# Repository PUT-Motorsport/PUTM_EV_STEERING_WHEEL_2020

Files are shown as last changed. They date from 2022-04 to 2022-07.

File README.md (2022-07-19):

# PUTM_EV_STEERING_WHEEL_2022

An overview of how I see this thing working:
kiera_schemat_blokowy_v2 (1)

* ~~Data gathered from IMU will be calculated into degrees and stored in buffers. These will be send out when the buffer is filled up.~~ 
* Interrupt will be triggered if a button is pressed. Then it will determine which button was pressed and send corresponding data. If, within specified, short time, there will occur another interrupt, then the programm will treat it as different action (two buttons pressed simultaneously). There will be 10 combinations: 4 single- and 6 simultaneous-presses.
* The scroll-like switches will trigger an interrupt if its position changes.

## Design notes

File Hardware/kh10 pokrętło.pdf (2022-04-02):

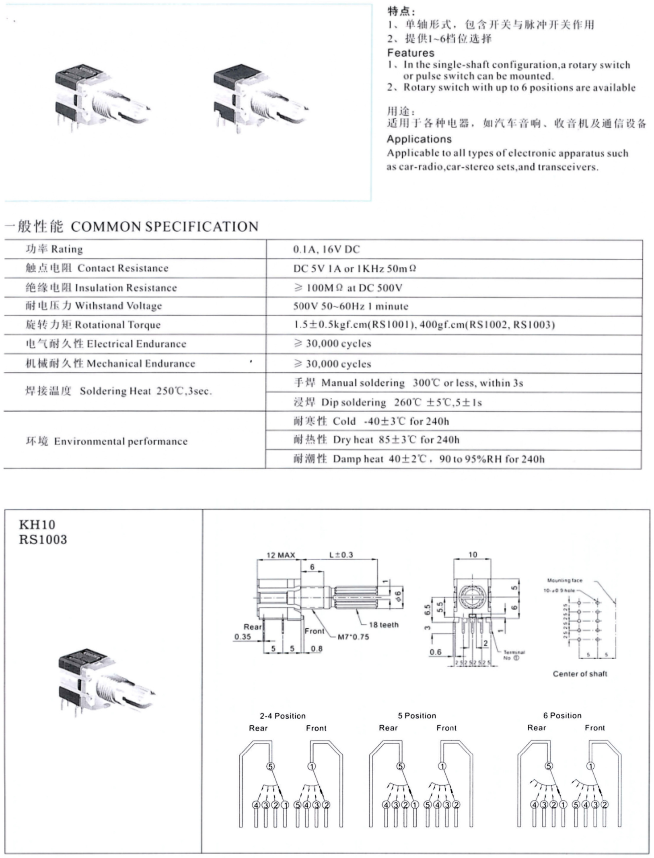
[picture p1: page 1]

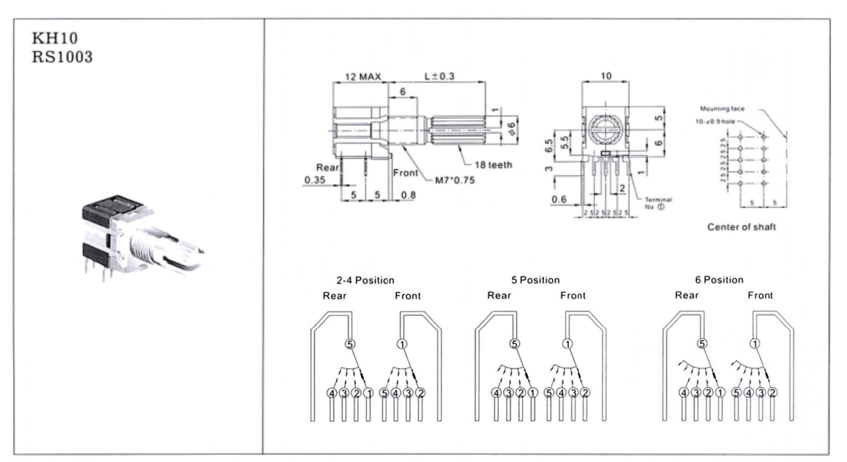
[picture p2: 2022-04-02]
Hardware/SW_DS.png

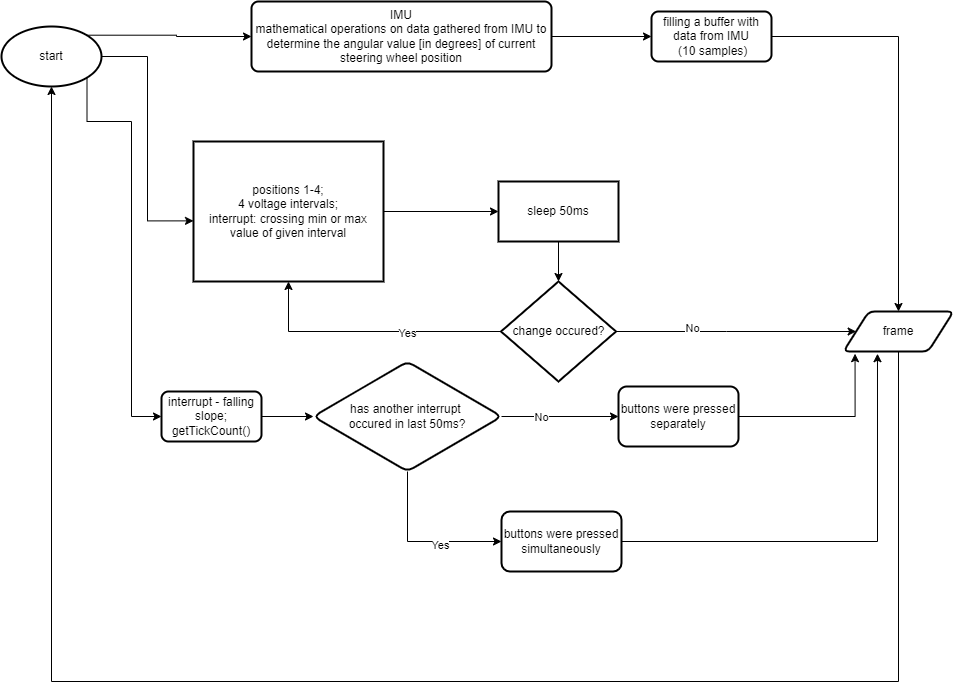
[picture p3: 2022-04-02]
Firmware/kiera_schemat_blokowy_v2 (1).png

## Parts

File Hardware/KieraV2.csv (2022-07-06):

Reference | Quantity | Value | Footprint | Datasheet
C1 C2 | 2 | 10pF | Capacitor_SMD:C_0603_1608Metric | ~
C10 C11 C14 C21 | 4 | 1uF | Capacitor_SMD:C_0603_1608Metric | ~
C3 C4 C5 C6 C7 C8 C9 C12 C13 C15 C16 C17 C18 C19 C20 C22 C23 C24 C25 C26 C27 C28 C29 C30 C31 C32 C33 C34 | 28 | 100nF | Capacitor_SMD:C_0603_1608Metric | ~
D1 D5 D6 D7 D8 D9 | 6 | LED | Diode_SMD:D_0805_2012Metric_Castellated | ~
D2 | 1 | D_Zener | Diode_SMD:D_SMB | ~
D3 | 1 | PESD2CAN.215 | Package_TO_SOT_SMD:SOT-23 | https://pl.mouser.com/datasheet/2/916/PESD2CAN-1320343.pdf
D4 | 1 | D_TVS | Diode_SMD:D_1210_3225Metric | https://www.tme.eu/Document/480040166f76761f76124a50403ca5aa/esd3b5v0ws.pdf
F1 | 1 | Fuse_Small | Fuse:Fuse_1206_3216Metric | ~
FB1 FB2 FB3 FB4 | 4 | 60R@100MHz | Inductor_SMD:L_0603_1608Metric | ~
J1 | 1 | Conn_01x04_Male | Connector_Wire:SolderWire-0.25sqmm_1x04_P4.2mm_D0.65mm_OD1.7mm_Relief | ~
J2 | 1 | Conn_01x06_Male | Connector_PinHeader_2.54mm:PinHeader_1x06_P2.54mm_Vertical | ~
JP1 | 1 | CAN_termination_jumper | Connector_PinHeader_2.54mm:PinHeader_1x02_P2.54mm_Vertical | ~
L1 | 1 | L_Core_Ferrite_Small | Inductor_SMD:L_0805_2012Metric | https://pl.mouser.com/datasheet/2/281/ENFA0003-1915778.pdf
NT1 | 1 | Net-Tie | NetTie:NetTie-2_SMD_Pad0.5mm | ~
R1 R3 R5 R7 R9 R12 R13 R14 R15 R18 R22 R23 R24 R25 R28 R30 R32 R34 R35 R36 R37 R42 | 22 | 1k | Resistor_SMD:R_0603_1608Metric | ~
R2 R4 R6 R8 R10 R11 R16 R17 R26 R27 R29 R31 R33 R38 R39 R40 R41 | 17 | 10k | Resistor_SMD:R_0603_1608Metric | ~
R19 R20 | 2 | 0R | Resistor_SMD:R_0603_1608Metric | ~
R21 | 1 | 120R | Resistor_SMD:R_0603_1608Metric | ~
SW1 SW2 | 2 | SW_Rotary2x4 | Rotary_Encoder:SW_Rotary2x4 | https://www.piekarz.pl/21583-przelacznik-kh10-obrotowy-bistabilny-4xon-4-pozycje/
SW11 | 1 | SW_MEC_5G | Button_Switch_SMD:SW_SPST_Omron_B3FS-100xP | http://www.apem.com/int/index.php?controller=attachment&id_attachment=488
SW3 SW4 SW5 SW6 SW7 SW8 SW9 SW10 | 8 | SW_Push | Button_Switch_THT:MyPushbuttonSwitch | ~
U1 | 1 | STM32L4P5RET6 | Package_QFP:LQFP-64_10x10mm_P0.5mm | https://www.st.com/en/microcontrollers-microprocessors/stm32l4p5re.html#documentation
U2 | 1 | LM1117-3.3 | Package_TO_SOT_SMD:SOT-23 | https://www.mouser.pl/ProductDetail/Microchip-Technology/MCP1799T-3302H-TT?qs=BJlw7L4Cy78EAGTR6Iuibw%3D%3D
U3 | 1 | IMS330DHCX | PUTM_Kicad_FOOTPRINTS:LGA-14_3x2.5mm_P0.5mm_LayoutBorder3x4y | www.st.com/resource/en/datasheet/lsm6ds3.pdf
U4 | 1 | ATA6561-GAQW-N | Package_SO:SOIC-8_3.9x4.9mm_P1.27mm | https://pl.mouser.com/datasheet/2/268/ATA6560_ATA6561_High_Speed_CAN_Transceiver_DS20005-1384933.pdf
Y1 | 1 | Crystal_GND24 | Crystal:Crystal_SMD_2520-4Pin_2.5x2.0mm | https://pl.mouser.com/datasheet/2/122/ECX_2236B2-2400583.pdf

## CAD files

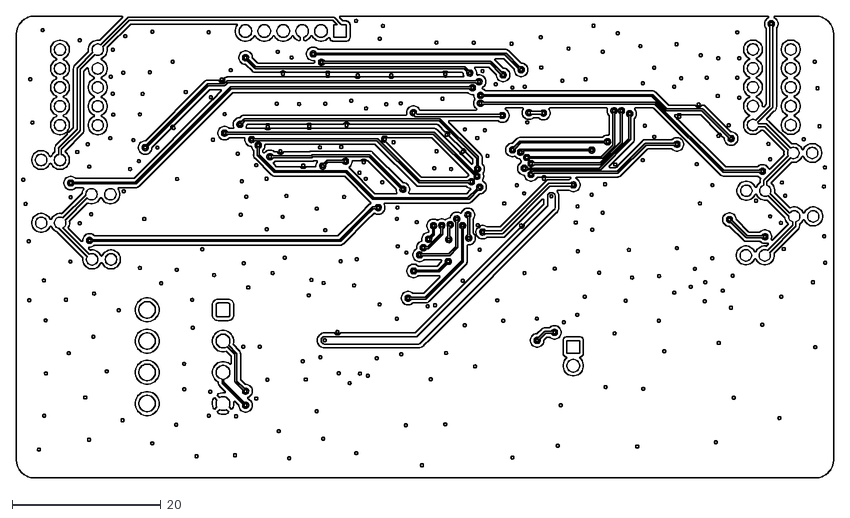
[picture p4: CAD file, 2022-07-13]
Hardware/SteeringWheelGerber/KieraV2-B_Cu.dxf
109.9 x 62.1

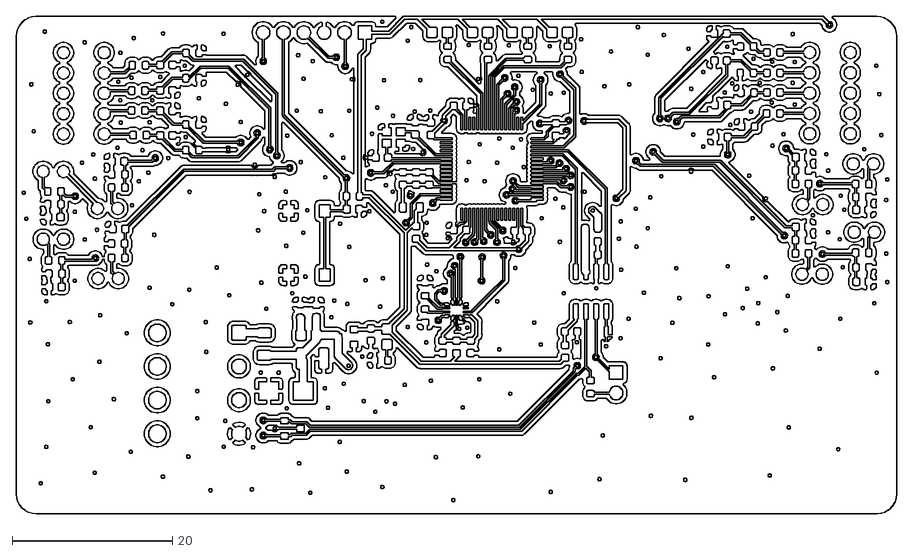
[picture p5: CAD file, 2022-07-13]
Hardware/SteeringWheelGerber/KieraV2-F_Cu.dxf
109.9 x 62.1

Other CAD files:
Hardware/SteeringWheelGerber/KieraV2-B_Mask.dxf
Hardware/SteeringWheelGerber/KieraV2-B_SilkS.dxf
Hardware/SteeringWheelGerber/KieraV2-F_Mask.dxf
Hardware/Stencil/KieraV2-F_Paste.dxf

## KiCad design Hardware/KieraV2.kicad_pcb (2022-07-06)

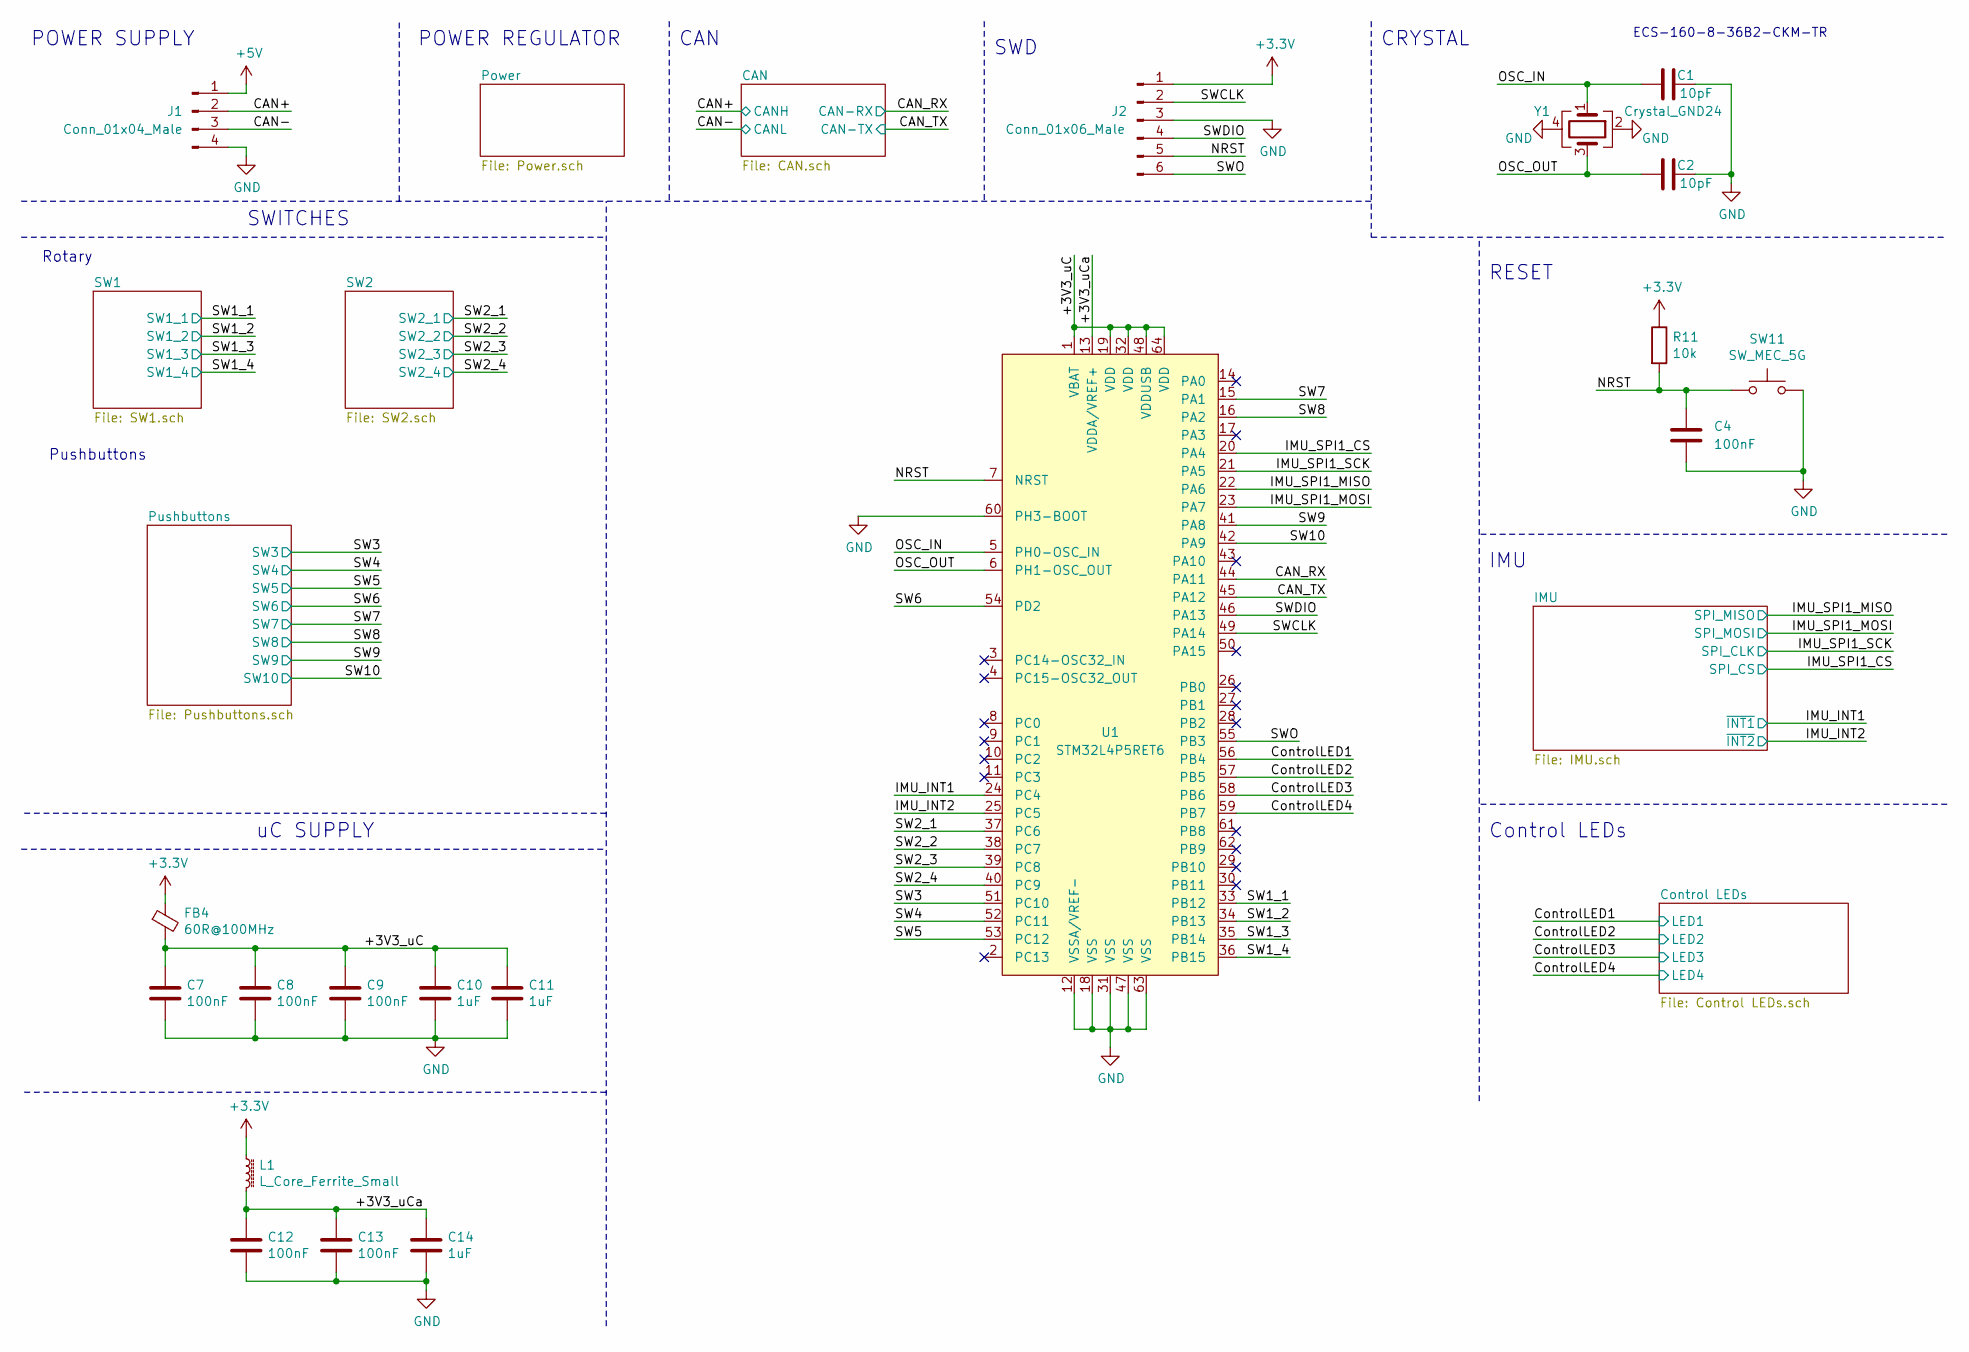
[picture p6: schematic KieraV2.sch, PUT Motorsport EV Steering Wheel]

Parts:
C1, C2: 10pF; C_0603_1608Metric
C4, C7, C8, C9, C12, C13: 100nF; C_0603_1608Metric
C10, C11, C14: 1uF; C_0603_1608Metric
FB4: 60R@100MHz; L_0603_1608Metric
J1: Conn_01x04_Male; SolderWire-0.25sqmm_1x04_P4.2mm_D0.65mm_OD1.7mm_Relief
J2: Conn_01x06_Male; PinHeader_1x06_P2.54mm_Vertical
L1: L_Core_Ferrite_Small; L_0805_2012Metric
R11: 10k; R_0603_1608Metric
SW11: SW_MEC_5G; SW_SPST_Omron_B3FS-100xP
U1: STM32L4P5RET6; LQFP-64_10x10mm_P0.5mm
Y1: Crystal_GND24; Crystal_SMD_2520-4Pin_2.5x2.0mm

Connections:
+5V: J1.1; also elsewhere on the board
/+3V3_uC: C7.1, C8.1, C9.1, C10.1, C11.1, FB4.2, U1.1 (VBAT), U1.19 (VDD), U1.32 (VDD), U1.48 (VDDUSB), U1.64 (VDD)
/+3V3_uCa: C12.1, C13.1, C14.1, L1.2, U1.13 (VDDA/VREF+)
/CAN+: J1.2; also elsewhere on the board
/CAN-: J1.3; also elsewhere on the board
/CAN_RX: U1.44 (PA11); also elsewhere on the board
/CAN_TX: U1.45 (PA12); also elsewhere on the board
/ControlLED1: U1.56 (PB4); also elsewhere on the board
/ControlLED2: U1.57 (PB5); also elsewhere on the board
/ControlLED3: U1.58 (PB6); also elsewhere on the board
/ControlLED4: U1.59 (PB7); also elsewhere on the board
/IMU_INT1: U1.24 (PC4); also elsewhere on the board
/IMU_INT2: U1.25 (PC5); also elsewhere on the board
/IMU_SPI1_CS: U1.20 (PA4); also elsewhere on the board
/IMU_SPI1_MISO: U1.22 (PA6); also elsewhere on the board
/IMU_SPI1_MOSI: U1.23 (PA7); also elsewhere on the board
/IMU_SPI1_SCK: U1.21 (PA5); also elsewhere on the board
/NRST: C4.1, J2.5, R11.2, SW11.1 (A), SW11.2 (A), U1.7 (NRST)
/OSC_IN: C1.1, U1.5 (PH0-OSC_IN), Y1.1
/OSC_OUT: C2.1, U1.6 (PH1-OSC_OUT), Y1.3
/SW1_1: U1.33 (PB12); also elsewhere on the board
/SW1_2: U1.34 (PB13); also elsewhere on the board
/SW1_3: U1.35 (PB14); also elsewhere on the board
/SW1_4: U1.36 (PB15); also elsewhere on the board
/SW2_1: U1.37 (PC6); also elsewhere on the board
/SW2_2: U1.38 (PC7); also elsewhere on the board
/SW2_3: U1.39 (PC8); also elsewhere on the board
/SW2_4: U1.40 (PC9); also elsewhere on the board
/SW3: U1.51 (PC10); also elsewhere on the board
/SW4: U1.52 (PC11); also elsewhere on the board
/SW5: U1.53 (PC12); also elsewhere on the board
/SW6: U1.54 (PD2); also elsewhere on the board
/SW7: U1.15 (PA1); also elsewhere on the board
/SW8: U1.16 (PA2); also elsewhere on the board
/SW9: U1.41 (PA8); also elsewhere on the board
/SW10: U1.42 (PA9); also elsewhere on the board
/SWCLK: J2.2, U1.49 (PA14)
/SWDIO: J2.4, U1.46 (PA13)
/SWO: J2.6, U1.55 (PB3)
GND: C1.2, C2.2, C4.2, C7.2, C8.2, C9.2, C10.2, C11.2, C12.2, C13.2, C14.2, J1.4, J2.3, SW11.3 (B), SW11.4 (B), U1.12 (VSSA/VREF-), U1.18 (VSS), U1.31 (VSS), U1.47 (VSS), U1.60 (PH3-BOOT), U1.63 (VSS), Y1.2, Y1.4; also elsewhere on the board

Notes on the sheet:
SWD
CAN
POWER REGULATOR
POWER SUPPLY
uC SUPPLY
CRYSTAL
RESET
SWITCHES
IMU
Rotary
ECS-160-8-36B2-CKM-TR
Pushbuttons
Control LEDs

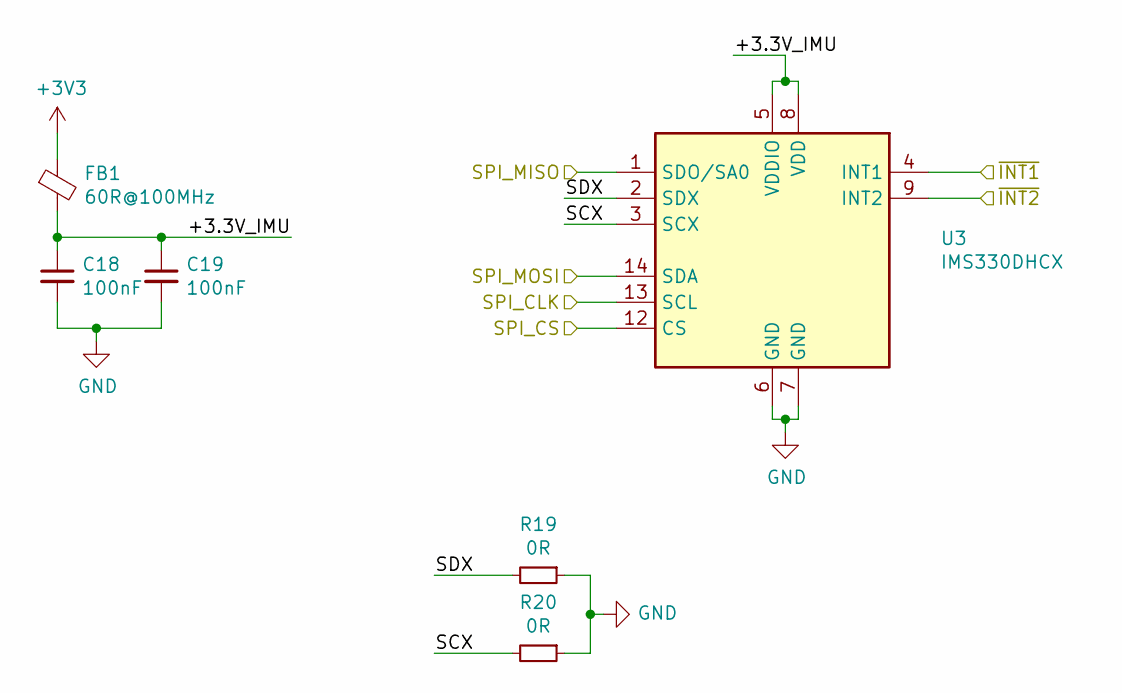
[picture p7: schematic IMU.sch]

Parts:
C18, C19: 100nF; C_0603_1608Metric
FB1: 60R@100MHz; L_0603_1608Metric
R19, R20: 0R; R_0603_1608Metric
U3: IMS330DHCX; LGA-14_3x2.5mm_P0.5mm_LayoutBorder3x4y

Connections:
/IMU/+3.3V_IMU: C18.1, C19.1, FB1.2, U3.5 (VDDIO), U3.8 (VDD)
/IMU/SCX: R20.2, U3.3 (SCX)
/IMU/SDX: R19.2, U3.2 (SDX)
/IMU_INT1: U3.4 (INT1); also elsewhere on the board
/IMU_INT2: U3.9 (INT2); also elsewhere on the board
/IMU_SPI1_CS: U3.12 (CS); also elsewhere on the board
/IMU_SPI1_MISO: U3.1 (SDO/SA0); also elsewhere on the board
/IMU_SPI1_MOSI: U3.14 (SDA); also elsewhere on the board
/IMU_SPI1_SCK: U3.13 (SCL); also elsewhere on the board
GND: C18.2, C19.2, R19.1, R20.1, U3.6 (GND), U3.7 (GND); also elsewhere on the board

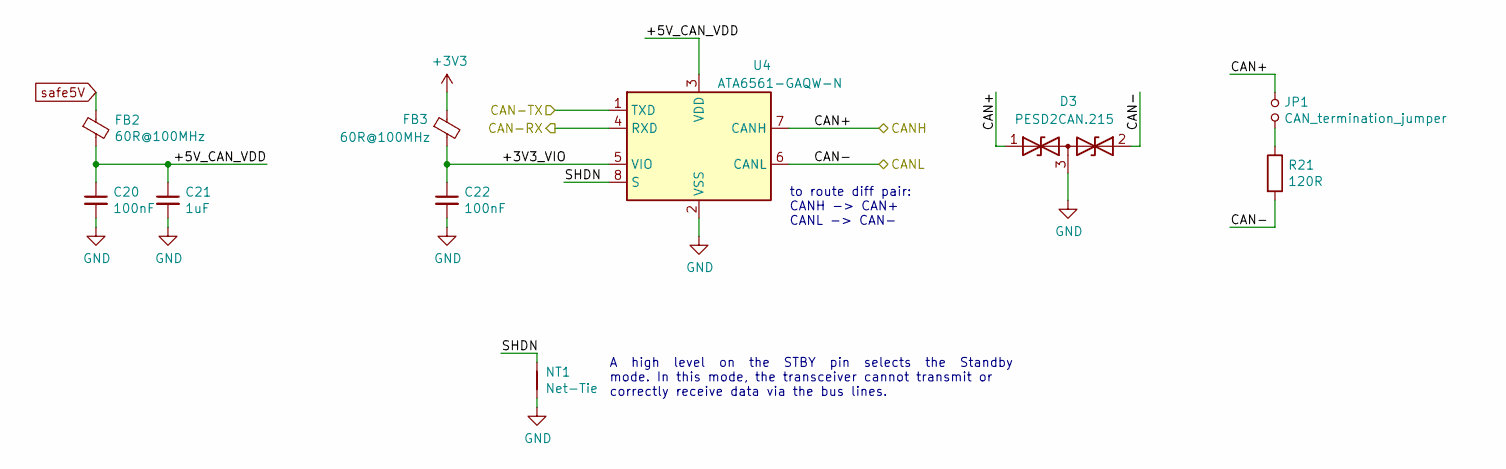
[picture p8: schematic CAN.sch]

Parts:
C20, C22: 100nF; C_0603_1608Metric
C21: 1uF; C_0603_1608Metric
D3: PESD2CAN.215; SOT-23
FB2, FB3: 60R@100MHz; L_0603_1608Metric
JP1: CAN_termination_jumper; PinHeader_1x02_P2.54mm_Vertical
NT1: Net-Tie; NetTie-2_SMD_Pad0.5mm
R21: 120R; R_0603_1608Metric
U4: ATA6561-GAQW-N; SOIC-8_3.9x4.9mm_P1.27mm

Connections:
/CAN+: D3.1 (A1), JP1.1, U4.7 (CANH); also elsewhere on the board
/CAN-: D3.2 (A2), R21.2, U4.6 (CANL); also elsewhere on the board
/CAN/+3V3_VIO: C22.1, FB3.2, U4.5 (VIO)
/CAN/+5V_CAN_VDD: C20.1, C21.1, FB2.2, U4.3 (VDD)
/CAN/SHDN: NT1.1, U4.8 (S)
/CAN_RX: U4.4 (RXD); also elsewhere on the board
/CAN_TX: U4.1 (TXD); also elsewhere on the board
GND: C20.2, C21.2, C22.2, D3.3 (common), NT1.2, U4.2 (VSS); also elsewhere on the board
unnamed: JP1.2, R21.1
safe5V: FB2.1; also elsewhere on the board

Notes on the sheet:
to route diff pair: CANH -> CAN+ CANL -> CAN-
A high level on the STBY pin selects the Standby mode. In this mode, the transceiver cannot transmit or correctly receive data via the bus lines.

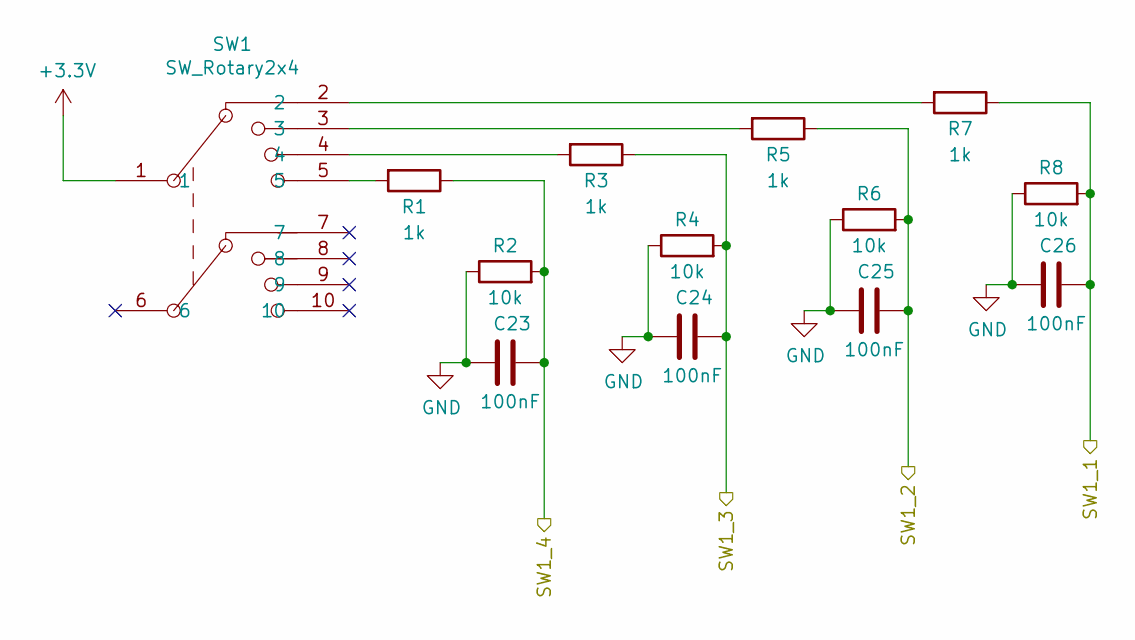
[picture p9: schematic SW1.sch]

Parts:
C23, C24, C25, C26: 100nF; C_0603_1608Metric
R1, R3, R5, R7: 1k; R_0603_1608Metric
R2, R4, R6, R8: 10k; R_0603_1608Metric
SW1: SW_Rotary2x4

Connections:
/SW1_1: C26.1, R7.1, R8.2; also elsewhere on the board
/SW1_2: C25.1, R5.1, R6.2; also elsewhere on the board
/SW1_3: C24.1, R3.1, R4.2; also elsewhere on the board
/SW1_4: C23.1, R1.1, R2.2; also elsewhere on the board
GND: C23.2, C24.2, C25.2, C26.2, R2.1, R4.1, R6.1, R8.1; also elsewhere on the board
unnamed: R1.2, SW1.5
unnamed: R3.2, SW1.4
unnamed: R5.2, SW1.3
unnamed: R7.2, SW1.2

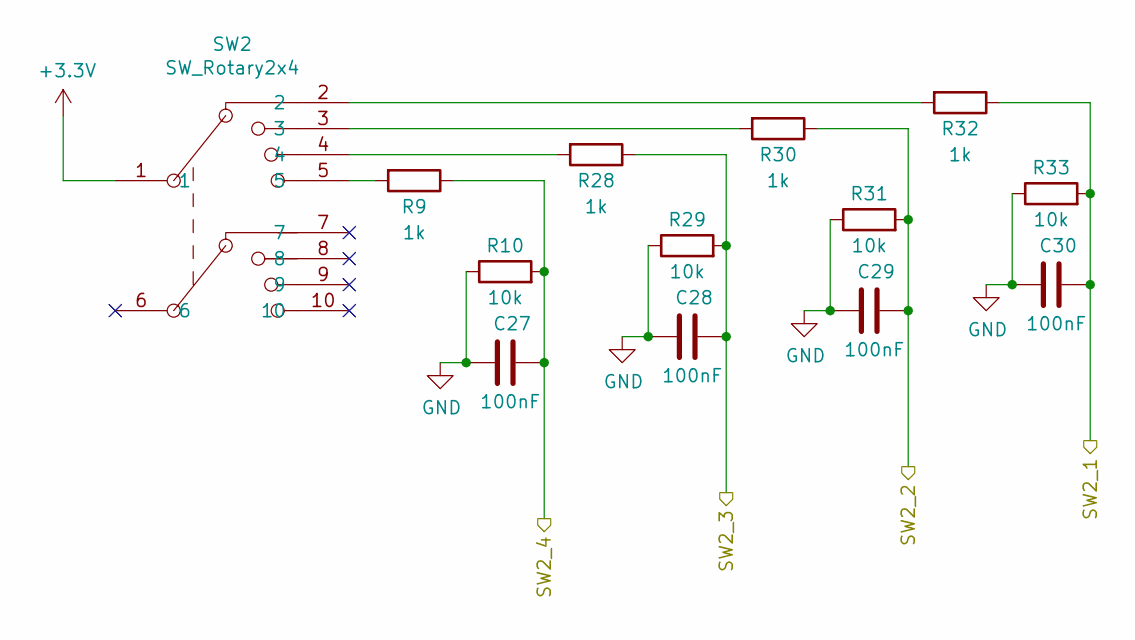
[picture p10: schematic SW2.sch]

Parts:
C27, C28, C29, C30: 100nF; C_0603_1608Metric
R9, R28, R30, R32: 1k; R_0603_1608Metric
R10, R29, R31, R33: 10k; R_0603_1608Metric
SW2: SW_Rotary2x4

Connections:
/SW2_1: C30.1, R32.1, R33.2; also elsewhere on the board
/SW2_2: C29.1, R30.1, R31.2; also elsewhere on the board
/SW2_3: C28.1, R28.1, R29.2; also elsewhere on the board
/SW2_4: C27.1, R9.1, R10.2; also elsewhere on the board
GND: C27.2, C28.2, C29.2, C30.2, R10.1, R29.1, R31.1, R33.1; also elsewhere on the board
unnamed: R9.2, SW2.5
unnamed: R28.2, SW2.4
unnamed: R30.2, SW2.3
unnamed: R32.2, SW2.2

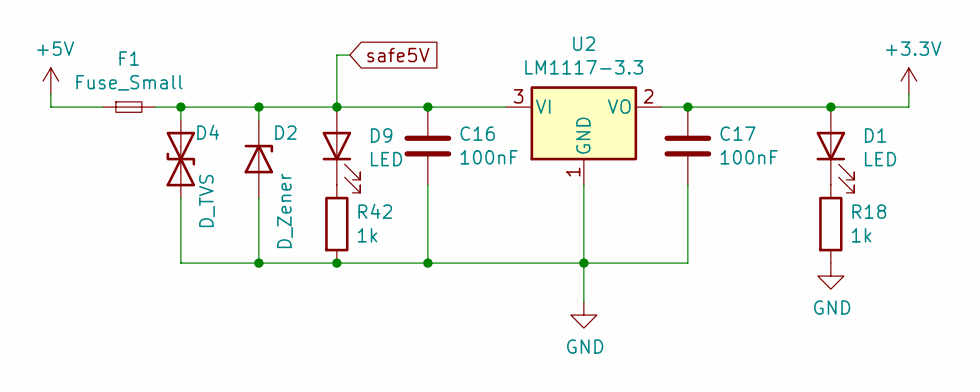
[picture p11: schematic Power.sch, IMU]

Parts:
C16, C17: 100nF; C_0603_1608Metric
D1, D9: LED; D_0805_2012Metric_Castellated
D2: D_Zener; D_SMB
D4: D_TVS; D_1210_3225Metric
F1: Fuse_Small; Fuse_1206_3216Metric
R18, R42: 1k; R_0603_1608Metric
U2: LM1117-3.3; SOT-23

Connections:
+5V: F1.1; also elsewhere on the board
GND: C16.2, C17.2, D2.2 (A), D4.1 (A1), R18.2, R42.2, U2.1 (GND); also elsewhere on the board
unnamed: D1.1 (K), R18.1
unnamed: D9.1 (K), R42.1
safe5V: C16.1, D2.1 (K), D4.2 (A2), D9.2 (A), F1.2, U2.3 (VI); also elsewhere on the board

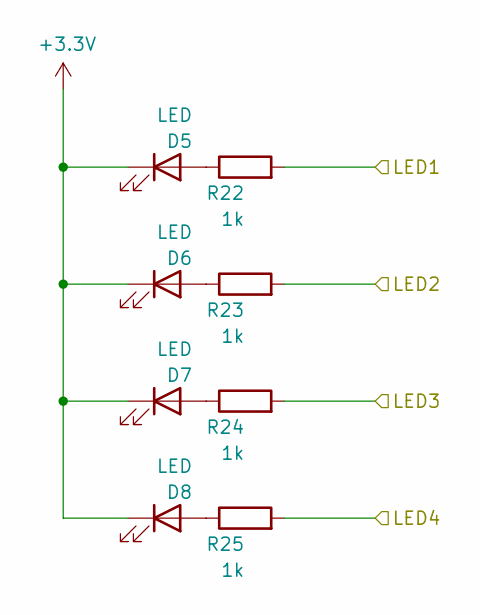
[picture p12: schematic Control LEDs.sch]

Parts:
D5, D6, D7, D8: LED; D_0805_2012Metric_Castellated
R22, R23, R24, R25: 1k; R_0603_1608Metric

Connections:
/ControlLED1: R22.2; also elsewhere on the board
/ControlLED2: R23.2; also elsewhere on the board
/ControlLED3: R24.2; also elsewhere on the board
/ControlLED4: R25.2; also elsewhere on the board
unnamed: D5.2 (A), R22.1
unnamed: D6.2 (A), R23.1
unnamed: D7.2 (A), R24.1
unnamed: D8.2 (A), R25.1

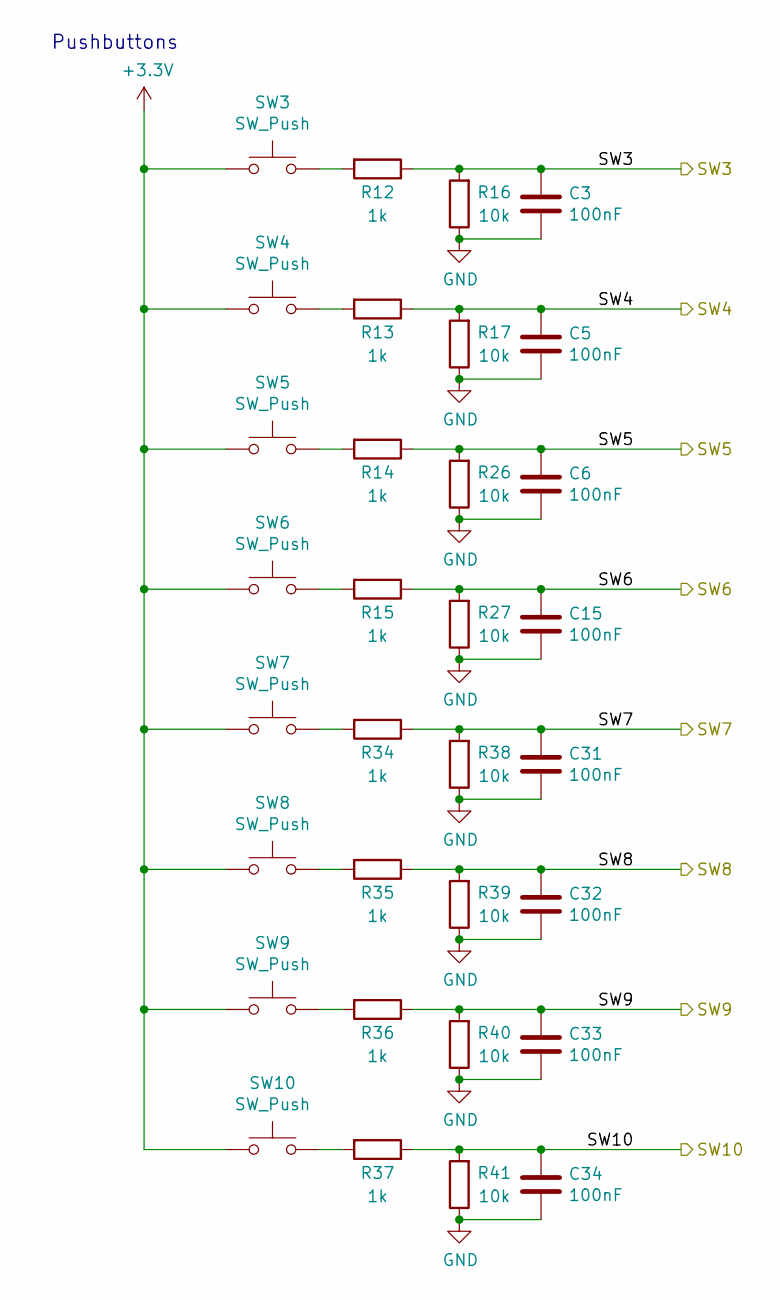
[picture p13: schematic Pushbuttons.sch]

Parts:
C3, C5, C6, C15, C31, C32, C33, C34: 100nF; C_0603_1608Metric
R12, R13, R14, R15, R34, R35, R36, R37: 1k; R_0603_1608Metric
R16, R17, R26, R27, R38, R39, R40, R41: 10k; R_0603_1608Metric
SW3, SW4, SW5, SW6, SW7, SW8, SW9, SW10: SW_Push; MyPushbuttonSwitch

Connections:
/SW3: C3.1, R12.1, R16.2; also elsewhere on the board
/SW4: C5.1, R13.1, R17.2; also elsewhere on the board
/SW5: C6.1, R14.1, R26.2; also elsewhere on the board
/SW6: C15.1, R15.1, R27.2; also elsewhere on the board
/SW7: C31.1, R34.1, R38.2; also elsewhere on the board
/SW8: C32.1, R35.1, R39.2; also elsewhere on the board
/SW9: C33.1, R36.1, R40.2; also elsewhere on the board
/SW10: C34.1, R37.1, R41.2; also elsewhere on the board
GND: C3.2, C5.2, C6.2, C15.2, C31.2, C32.2, C33.2, C34.2, R16.1, R17.1, R26.1, R27.1, R38.1, R39.1, R40.1, R41.1; also elsewhere on the board
unnamed: R12.2, SW3.2
unnamed: R13.2, SW4.2
unnamed: R14.2, SW5.2
unnamed: R15.2, SW6.2
unnamed: R34.2, SW7.2
unnamed: R35.2, SW8.2
unnamed: R36.2, SW9.2
unnamed: R37.2, SW10.2

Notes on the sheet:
Pushbuttons

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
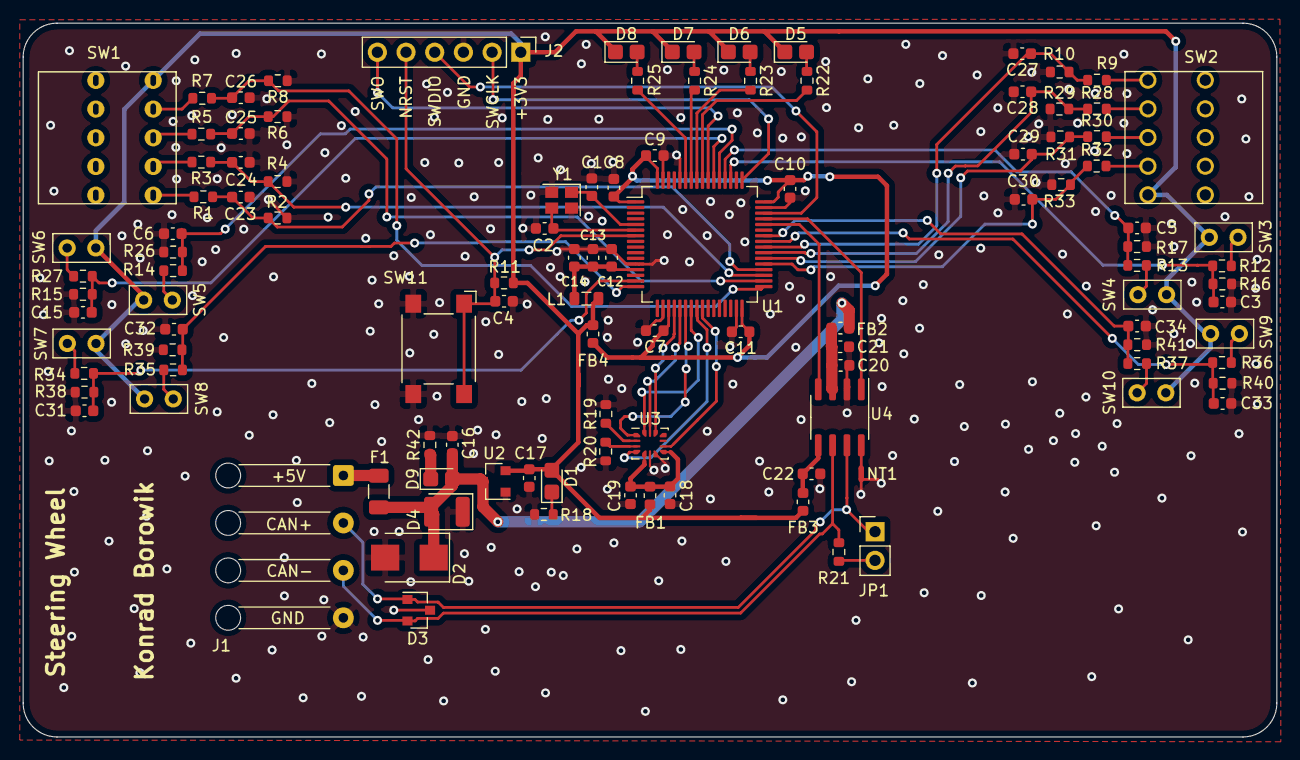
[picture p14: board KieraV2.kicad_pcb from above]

Board: 2 copper layers, 111.0 x 63.2 mm, 111 parts (0 on the bottom side), 71 nets.

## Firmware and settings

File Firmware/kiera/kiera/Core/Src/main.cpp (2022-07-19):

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
/* Includes ------------------------------------------------------------------*/
#include "main.h"

/* USER CODE BEGIN Includes */
#include <stdio.h>
#include <string.h>
#include <stdbool.h>
#include "PUTM_EV_CAN_LIBRARY/lib/can_interface.hpp"

/* USER CODE END Includes */

 CAN_HandleTypeDef hcan1;

/* USER CODE BEGIN PV */
uint32_t timer;

bool sw3_pressed, sw4_pressed, sw5_pressed, sw6_pressed;
PUTM_CAN::scrollStates last_left_scroll_state;
PUTM_CAN::scrollStates last_right_scroll_state;
PUTM_CAN::buttonStates last_button_pressed;
bool scroll_activated = 0;
int i = 0;
void send_frame(PUTM_CAN::buttonStates);
/* USER CODE END PV */

void SystemClock_Config(void);
static void MX_GPIO_Init(void);
static void MX_CAN1_Init(void);
/**
  * @brief  The application entry point.
  * @retval int
  */
int main(void)
{
  /* MCU Configuration--------------------------------------------------------*/

  /* Reset of all peripherals, Initializes the Flash interface and the Systick. */
  HAL_Init();

  /* Configure the system clock */
  SystemClock_Config();

  /* Initialize all configured peripherals */
  MX_GPIO_Init();
  MX_CAN1_Init();
  /* USER CODE BEGIN 2 */

  CAN_FilterTypeDef sFilterConfig;
  sFilterConfig.FilterBank = 0;
  sFilterConfig.FilterMode = CAN_FILTERMODE_IDMASK;
  sFilterConfig.FilterScale = CAN_FILTERSCALE_32BIT;
  sFilterConfig.FilterIdHigh = 0x0000;
  sFilterConfig.FilterIdLow = 0x0000;
  sFilterConfig.FilterMaskIdHigh = 0x0000;
  sFilterConfig.FilterMaskIdLow = 0x0000;
  sFilterConfig.FilterFIFOAssignment = CAN_RX_FIFO0;
  sFilterConfig.FilterActivation = ENABLE;


	if (HAL_CAN_ConfigFilter(&hcan1, &sFilterConfig) != HAL_OK) {
		Error_Handler();
	}

	if (HAL_CAN_Start(&hcan1) != HAL_OK) {
		Error_Handler();
	}

	if (HAL_CAN_ActivateNotification(&hcan1, CAN_IT_RX_FIFO0_MSG_PENDING | CAN_IT_TX_MAILBOX_EMPTY) != HAL_OK) {
		Error_Handler();
	}

  HAL_CAN_ActivateNotification(&hcan1, CAN_IT_RX_FIFO0_MSG_PENDING);
  uint32_t timer = HAL_GetTick();
  /* USER CODE END 2 */

  /* Infinite loop */
  /* USER CODE BEGIN WHILE */
  while (1)
  {
	  i++;
    /* USER CODE END WHILE */

    /* USER CODE BEGIN 3 */
	  if (sw3_pressed or sw4_pressed or sw5_pressed or sw6_pressed) {
		  wait_for_second_button();
	  }

	  if (scroll_activated) {
		  send_frame(PUTM_CAN::buttonStates::not_pressed);
	  }

	  if (timer + 500 < HAL_GetTick())
	  {
		  heartbeat();
		  timer = HAL_GetTick();
	  }

  }
  /* USER CODE END 3 */
}

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
/* USER CODE BEGIN 4 */
void HAL_GPIO_EXTI_Callback(uint16_t GPIO_Pin)
{
//	timer = HAL_GetTick();
	PUTM_CAN::Steering_Wheel_event scroll_state{};

	if (GPIO_Pin == SW3_Pin)
	{
		sw3_pressed = 1;
	} else if (GPIO_Pin == SW4_Pin)
	{
		sw4_pressed = 1;
	} else if (GPIO_Pin == SW5_Pin)
	{
		sw5_pressed = 1;
	} else if (GPIO_Pin == SW6_Pin)
	{
		sw6_pressed = 1;
	} else {
		if (GPIO_Pin == SW1_1_Pin)
		{
			last_left_scroll_state = PUTM_CAN::scrollStates::scroll_1;
		} else if (GPIO_Pin == SW1_2_Pin)
		{
			last_left_scroll_state = PUTM_CAN::scrollStates::scroll_2;
		} else if (GPIO_Pin == SW1_3_Pin)
		{
			last_left_scroll_state = PUTM_CAN::scrollStates::scroll_3;
		} else if (GPIO_Pin == SW1_4_Pin)
		{
			last_left_scroll_state = PUTM_CAN::scrollStates::scroll_4;
		} else if (GPIO_Pin == SW2_1_Pin)
		{
			last_right_scroll_state = PUTM_CAN::scrollStates::scroll_1;
		} else if (GPIO_Pin == SW2_2_Pin)
		{
			last_right_scroll_state = PUTM_CAN::scrollStates::scroll_2;
		} else if (GPIO_Pin == SW2_3_Pin)
		{
			last_right_scroll_state = PUTM_CAN::scrollStates::scroll_3;
		} else if (GPIO_Pin == SW2_4_Pin)
		{
			last_right_scroll_state = PUTM_CAN::scrollStates::scroll_4;
		}

		scroll_activated = 1;
	}


}

void send_frame(PUTM_CAN::buttonStates button)
{
	PUTM_CAN::Steering_Wheel_event payload{};

	payload.l_s_1 = last_left_scroll_state;
	payload.r_s_1 = last_right_scroll_state;
	payload.button = button;
	auto steering_wheel_frame = PUTM_CAN::Can_tx_message<PUTM_CAN::Steering_Wheel_event>
		(payload, PUTM_CAN::can_tx_header_STEERING_WHEEL_EVENT);

	if (HAL_OK not_eq steering_wheel_frame.send(hcan1)) {
		HAL_GPIO_TogglePin(ControlLed1_GPIO_Port, ControlLed1_Pin);
	}

	reset_flags();
}

void heartbeat()
{

	PUTM_CAN::Steering_Wheel_main pcb_alive{0, PUTM_CAN::Steering_Wheel_states::OK};

	auto steering_wheel_heartbeat = PUTM_CAN::Can_tx_message<PUTM_CAN::Steering_Wheel_main>
	(pcb_alive, PUTM_CAN::can_tx_header_STEERING_WHEEL_MAIN);

 	steering_wheel_heartbeat.send(hcan1);

}

void wait_for_second_button()
{
	HAL_Delay(500);
	PUTM_CAN::buttonStates button = PUTM_CAN::buttonStates::not_pressed;

	if (sw3_pressed && sw4_pressed)	{
		button = PUTM_CAN::buttonStates::button3_4;
	} else if (sw3_pressed && sw5_pressed) {
		button = PUTM_CAN::buttonStates::button2_4;
	} else if (sw3_pressed && sw6_pressed) {
		button = PUTM_CAN::buttonStates::button1_4;
	} else if (sw4_pressed && sw5_pressed) {
		button = PUTM_CAN::buttonStates::button2_3;
		HAL_GPIO_TogglePin(ControlLed2_GPIO_Port, ControlLed2_Pin);
	} else if (sw4_pressed && sw6_pressed) {
		button = PUTM_CAN::buttonStates::button1_3;
	} else if (sw5_pressed && sw6_pressed) {
		button = PUTM_CAN::buttonStates::button1_2;
	} else if (sw3_pressed) {
		button = PUTM_CAN::buttonStates::button4;
	} else if (sw4_pressed) {
		button = PUTM_CAN::buttonStates::button3;
	} else if (sw5_pressed) {
		button = PUTM_CAN::buttonStates::button2;
	} else if (sw6_pressed) {
		button = PUTM_CAN::buttonStates::button1;
	}

	send_frame(button);

	reset_flags();
}

void reset_flags()
{
	sw3_pressed = 0;
	sw4_pressed = 0;
	sw5_pressed = 0;
	sw6_pressed = 0;
	scroll_activated = 0;
}

/* USER CODE END 4 */

/**
  * @brief  Period elapsed callback in non blocking mode
  * @note   This function is called  when TIM1 interrupt took place, inside
  * HAL_TIM_IRQHandler(). It makes a direct call to HAL_IncTick() to increment
  * a global variable "uwTick" used as application time base.
  * @param  htim : TIM handle
  * @retval None
  */
void HAL_TIM_PeriodElapsedCallback(TIM_HandleTypeDef *htim)
{
  if (htim->Instance == TIM1) {
    HAL_IncTick();
  }
}

/**
  * @brief  This function is executed in case of error occurrence.
  * @retval None
  */
void Error_Handler(void)
{
  /* USER CODE BEGIN Error_Handler_Debug */
  /* User can add his own implementation to report the HAL error return state */
  __disable_irq();
  while (1)
  {
  }
  /* USER CODE END Error_Handler_Debug */
}

#ifdef  USE_FULL_ASSERT
/**
  * @brief  Reports the name of the source file and the source line number
  *         where the assert_param error has occurred.
  * @param  file: pointer to the source file name
  * @param  line: assert_param error line source number
  * @retval None
  */
void assert_failed(uint8_t *file, uint32_t line)
{
  /* USER CODE BEGIN 6 */
  /* User can add his own implementation to report the file name and line number,
     ex: printf("Wrong parameters value: file %s on line %d\r\n", file, line) */
  /* USER CODE END 6 */
}
#endif /* USE_FULL_ASSERT */

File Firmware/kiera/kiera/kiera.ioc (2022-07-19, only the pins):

Mcu.UserName=STM32L4P5RETx
PA1.GPIO_Label=SW5
PA1.Signal=GPXTI1
PA11.Signal=CAN1_RX
PA12.Signal=CAN1_TX
PA4.Signal=SPI1_NSS
PA5.Signal=SPI1_SCK
PA6.Signal=SPI1_MISO
PA7.Signal=SPI1_MOSI
PB12.GPIO_Label=SW1_1
PB12.Signal=GPXTI12
PB13.GPIO_Label=SW1_2
PB13.Signal=GPXTI13
PB14.GPIO_Label=SW1_3
PB14.Signal=GPXTI14
PB15.GPIO_Label=SW1_4
PB15.Signal=GPXTI15
PB5.GPIO_Label=ControlLed3
PB5.Signal=GPIO_Output
PB6.GPIO_Label=ControlLed2
PB6.Signal=GPIO_Output
PB7.GPIO_Label=ControlLed1
PB7.Signal=GPIO_Output
PC10.GPIO_Label=SW3
PC10.Signal=GPXTI10
PC11.GPIO_Label=SW4
PC11.Signal=GPXTI11
PC4.Signal=GPXTI4
PC5.Signal=GPXTI5
PC6.GPIO_Label=SW2_1
PC6.Signal=GPXTI6
PC7.GPIO_Label=SW2_2
PC7.Signal=GPXTI7
PC8.GPIO_Label=SW2_3
PC8.Signal=GPXTI8
PC9.GPIO_Label=SW2_4
PC9.Signal=GPXTI9
PD2.GPIO_Label=SW6
PD2.Signal=GPXTI2

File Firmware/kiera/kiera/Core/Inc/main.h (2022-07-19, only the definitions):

#define SW5_Pin GPIO_PIN_1
#define SW5_GPIO_Port GPIOA
#define SW5_EXTI_IRQn EXTI1_IRQn
#define SW1_1_Pin GPIO_PIN_12
#define SW1_1_GPIO_Port GPIOB
#define SW1_1_EXTI_IRQn EXTI15_10_IRQn
#define SW1_2_Pin GPIO_PIN_13
#define SW1_2_GPIO_Port GPIOB
#define SW1_2_EXTI_IRQn EXTI15_10_IRQn
#define SW1_3_Pin GPIO_PIN_14
#define SW1_3_GPIO_Port GPIOB
#define SW1_3_EXTI_IRQn EXTI15_10_IRQn
#define SW1_4_Pin GPIO_PIN_15
#define SW1_4_GPIO_Port GPIOB
#define SW1_4_EXTI_IRQn EXTI15_10_IRQn
#define SW2_1_Pin GPIO_PIN_6
#define SW2_1_GPIO_Port GPIOC
#define SW2_1_EXTI_IRQn EXTI9_5_IRQn
#define SW2_2_Pin GPIO_PIN_7
#define SW2_2_GPIO_Port GPIOC
#define SW2_2_EXTI_IRQn EXTI9_5_IRQn
#define SW2_3_Pin GPIO_PIN_8
#define SW2_3_GPIO_Port GPIOC
#define SW2_3_EXTI_IRQn EXTI9_5_IRQn
#define SW2_4_Pin GPIO_PIN_9
#define SW2_4_GPIO_Port GPIOC
#define SW2_4_EXTI_IRQn EXTI9_5_IRQn
#define SW3_Pin GPIO_PIN_10
#define SW3_GPIO_Port GPIOC
#define SW3_EXTI_IRQn EXTI15_10_IRQn
#define SW4_Pin GPIO_PIN_11
#define SW4_GPIO_Port GPIOC
#define SW4_EXTI_IRQn EXTI15_10_IRQn
#define SW6_Pin GPIO_PIN_2
#define SW6_GPIO_Port GPIOD
#define SW6_EXTI_IRQn EXTI2_IRQn
#define ControlLed4_Pin GPIO_PIN_4
#define ControlLed4_GPIO_Port GPIOB
#define ControlLed3_Pin GPIO_PIN_5
#define ControlLed3_GPIO_Port GPIOB
#define ControlLed2_Pin GPIO_PIN_6
#define ControlLed2_GPIO_Port GPIOB
#define ControlLed1_Pin GPIO_PIN_7
#define ControlLed1_GPIO_Port GPIOB

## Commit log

2021-11-27 added .gitignore, SW_rotary_2x4
    [KieraV2.sch, Power.sch]
2021-11-27 added SWD pinout
    [KieraV2.sch]
2021-11-27 added VSS, connector for can and power
    [KieraV2.sch, Power.sch]
2021-11-27 finished power scheme and some cosmetics
    [KieraV2.sch, Power.sch]
2021-11-27 uC supply added
    [CAN.sch, KieraV2.sch]
2021-11-27 added reset button
    [CAN.sch, KieraV2.sch]
2021-11-27 ready to review
    [KieraV2.sch]
2021-11-28 removed resistor in crystal section
    [KieraV2.sch]
2021-11-28 10k resistor in reset
    [KieraV2.sch]
2021-11-30 changed resistor value in power scheme
    [Power.sch]
2021-11-30 RC added by pushbuttons, changed capacitors in uC supply
    [KieraV2.sch, Power.sch]
2021-12-08 changed global labels to local, added IMU
    [CAN.sch, KieraV2.sch, Power.sch]
2021-12-08 IMU.sch added
    [IMU.sch]
2021-12-08 added footprints, updated CAN, annotated symbols
    [CAN.sch, IMU.sch, KieraV2.sch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]
2021-12-08 added temp pushbutton footprint
    [IMU.sch, KieraV2.sch]
2021-12-08 small changes to footprints
    [KieraV2.sch]
2021-12-11 small changes to the electrical schematic, added footprints, first go at designing the pcb
    [CAN.sch, Control LEDs.sch, IMU.sch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]
2021-12-14 added button for starting procedure, changes to pcb layout pending
    [CAN.sch, Control LEDs.sch, IMU.sch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]
2021-12-15 controll leds are now groundend on uC, some changes of the pcb layout
    [Control LEDs.sch, KieraV2.kicad_pcb, KieraV2.sch]
2021-12-15 supplly lines are now thicc
    [KieraV2.kicad_pcb]
2021-12-15 little more changes
    [KieraV2.kicad_pcb]
2021-12-20 pcb layout
    [KieraV2.kicad_pcb]
2021-12-21 redesigned layout
    [KieraV2.kicad_pcb]
2021-12-21 power supply connector is now a micro-fit
    [KieraV2.kicad_pcb, KieraV2.sch]
2021-12-21 tiny adjustments
    [KieraV2.kicad_pcb]
2021-12-28 rotary switches moved down
    [KieraV2.kicad_pcb]
2021-12-28 IMU centered
    [KieraV2.kicad_pcb]
2021-12-28 cutouts for quickrelease
    [KieraV2.kicad_pcb]
2021-12-28 labels adjusted
    [KieraV2.kicad_pcb]
2021-12-28 some more adjustments
    [KieraV2.kicad_pcb]
2021-12-28 symbol changed, bigger cable hole in the middle
    [Control LEDs.sch, KieraV2.kicad_pcb, SW1.sch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]
2021-12-28 bigger holes
    [KieraV2.kicad_pcb]
2021-12-28 more adjustments
    [KieraV2.kicad_pcb]
2022-01-06 redesigned PCB
    [KieraV2.kicad_pcb, SW1.sch, SW2.sch]
2022-01-06 moved labels on pcb
    [KieraV2.kicad_pcb]
2022-01-06 added logo
    [KieraV2.kicad_pcb]
2022-01-06 added mounting holes
    [KieraV2.kicad_pcb]
2022-01-07 moved mounting holes
    [KieraV2.kicad_pcb]
2022-01-07 dimensions added
    [KieraV2.kicad_pcb]
2022-01-07 hole adjustments
    [KieraV2.kicad_pcb]
2022-01-11 new input 'connector', rearrangement
    [KieraV2.kicad_pcb, KieraV2.sch]
2022-01-11 added logos
    [KieraV2.kicad_pcb]
2022-01-12 pcb changed
    [KieraV2.kicad_pcb]
2022-01-12 new changes
    [KieraV2.kicad_pcb]
2022-01-13 added gnd layers
    [KieraV2.kicad_pcb]
2022-01-13 changed imu footprint
    [KieraV2.kicad_pcb]
2022-01-17 added 6pin connector and somme labels
    [KieraV2.kicad_pcb, KieraV2.sch]
2022-01-24 added ground
    [KieraV2-B_Cu.gbl, KieraV2-B_Mask.gbs, KieraV2-B_Paste.gbp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]
2022-01-24 filled properly
    [KieraV2-B_Cu.gbl, KieraV2-B_Mask.gbs, KieraV2-B_Paste.gbp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]
2022-03-15 new flowchart
2022-04-02 fix - can rx&tx swapped
    [KieraV2.sch]
2022-04-02 fix - changed regulator model
    [Power.sch]
2022-04-04 can on pcb updated
    [KieraV2.kicad_pcb]
2022-05-10 wroking interrupts and dma
    [kiera Debug.cfg]
2022-05-13 configuration for second adc, new variables for more buttons/scrolls
2022-05-13 code for 4 buttons
2022-05-13 functionality for every switch, passing adc readings to function doesn't work
    [main.h]
2022-05-22 sending frames
2022-05-23 buttons send frames
2022-06-01 removed resistor ladder
    [SW1.sch, SW2.sch]
2022-06-01 rotary switches connected
    [KieraV2.sch]
2022-06-01 boot pin connected to gnd
    [KieraV2.sch]
2022-06-01 added more buttons
    [KieraV2.sch, Pushbuttons.sch, SW1.sch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]
2022-06-01 refilled zones
    [KieraV2.kicad_pcb]
2022-06-01 refilled gnd again
    [KieraV2.kicad_pcb]
2022-06-02 changed positions for buttons
    [KieraV2.kicad_pcb, KieraV2.sch, Pushbuttons.sch]
2022-06-15 added fuse
    [KieraV2.sch, Power.sch]
2022-06-15 updated pcb
    [CAN.sch, KieraV2.kicad_pcb, Power.sch]
2022-06-21 temporary firmware
    [KieraV2.kicad_pcb]
2022-06-21 compiled with 0 errors
    [main.cpp, main.h, temporary_kiera2.ioc]
2022-07-06 changed uC configuration
    [CAN.sch, KieraV2-F_Paste.dxf, KieraV2.csv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]
2022-07-06 sending frames from scrolls
2022-07-13 can setup
    [KieraV2-B_Cu.dxf, KieraV2-B_Mask.dxf, KieraV2-B_SilkS.dxf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]
2022-07-18 annotating last frame
2022-07-19 working communication with dash, buttons are 1-4 from left to right
2023-04-04 Revert "firmware overhaul"
    This reverts commit fc4f7325b2842b3143a277c0ec91c70f9f31444.
    [kiera.ioc, main.cpp, main.h]

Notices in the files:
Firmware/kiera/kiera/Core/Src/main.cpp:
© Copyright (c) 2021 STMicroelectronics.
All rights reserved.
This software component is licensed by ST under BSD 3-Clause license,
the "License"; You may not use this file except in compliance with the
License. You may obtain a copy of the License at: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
